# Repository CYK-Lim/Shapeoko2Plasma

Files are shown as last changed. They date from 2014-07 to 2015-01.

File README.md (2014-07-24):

```
Shapeoko 2
	NEMA 23 Mechanical Kit
	Z Axis Upgrade w/ NEMA 23
	Handle/Knob

Probotix
	RF Isolated CNC Breakout Board
	4x SideStep Bi-Polar Stepper Motor Driver
	4x HT23-260-4 Stepper Motor
	24Volt 6.5Amp Switching Power Supply
	6ft. DB25 Male-to-Male Cable
	3x 4" IDC Cable 10-pin
	2x 10PIN 12" IDC Adapter Cable

Hypertherm
	Powermax65
	RS485 Modbus ASCII communications card
	CNC Interface

PC
	Intel i5
	Ubuntu 12.04
	RTAI 3.2 Kernel
	LinuxCNC 2.6
	Parallel Port PCIe card
	RS485 serial port PCIe card
	SheetCAM TNG 6.1

Torch Height Control
	Seeeduino Mega V1.21
	Mesa THCAD Voltage to Frequency converter

Miscellaneous
	Automation Direct Solid state relay
	DIN Rail fuse holder and fuses
	Various cables (2 conductor, 4 conductor, 6 conductor shielded) 
	RS485 breakout board (Amazon)
	Automation Direct ferrule kit

Custom Software
	SheetCAM Post processor (lua)
	Custom M and O commands (Linuxcnc)
	Torch height controls (arduino)
	Modbus ASCII controls and HMI (pyModbus and pyvcp) 

Mechanical additions
	Frame (1”x3” .125” thick mild steel tubing, slots cut with 1/8" wide chop saw blade)
	Slats (1” .125” thick mild steel flats)
	Water basin (24 gauge mild steel sheet bent/welded/coated with Rubberizeit)

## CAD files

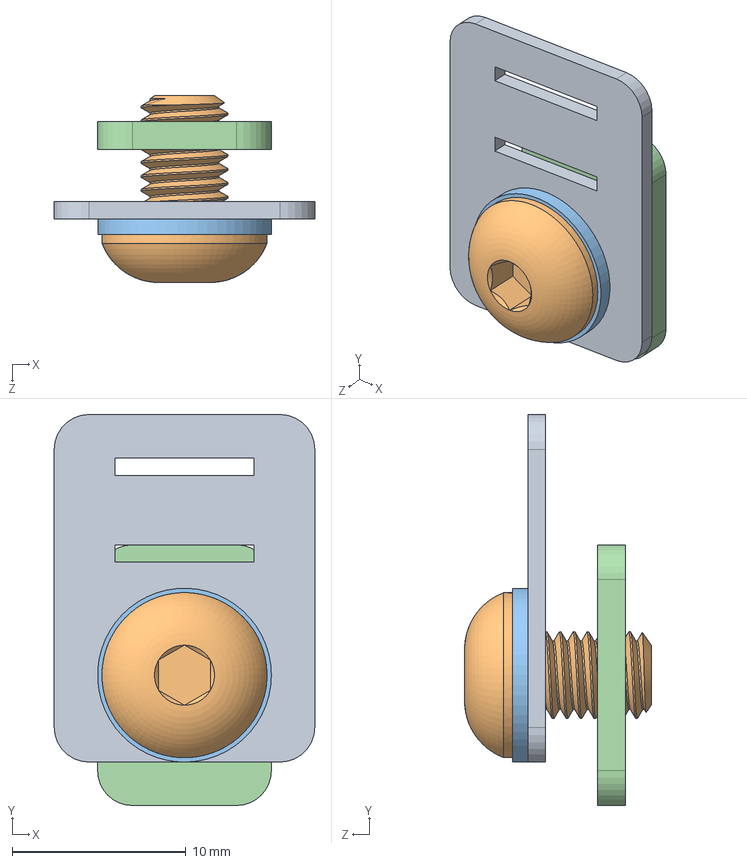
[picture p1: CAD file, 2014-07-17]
Solid Model/belt_clip_assembly.sldasm
15.0 x 22.5 x 10.7 mm
91239A222

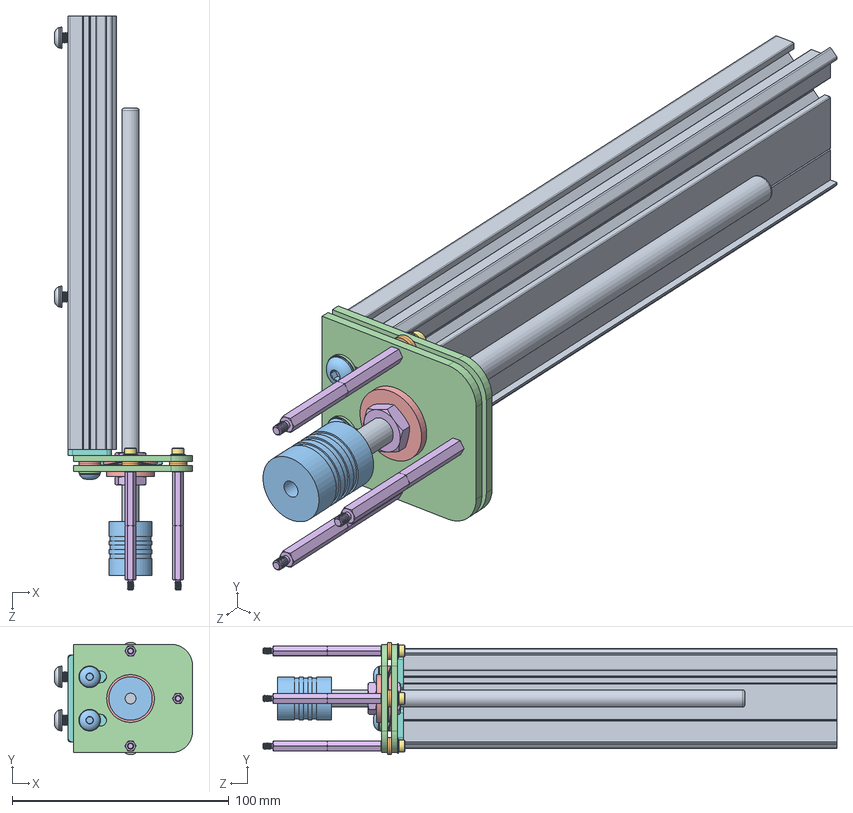
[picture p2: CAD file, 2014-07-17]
Solid Model/S2_Zaxis_500.sldasm
63.8 x 51.8 x 264.7 mm
z-mount_plates x 2
90695A040 x 2
z-axis shim
SM-H05
492-1101-ND x 6
91239A233 x 2
PSM5-01MM x 4
PSBS-50 x 3
9714K630

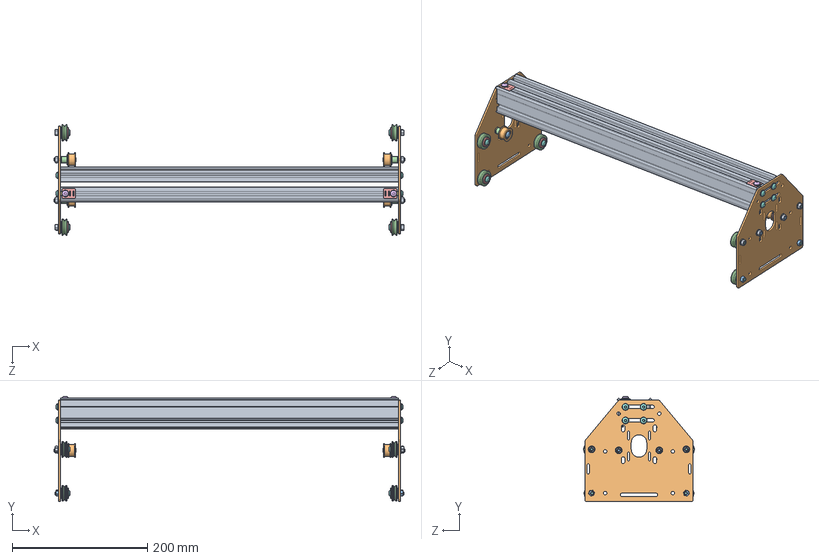
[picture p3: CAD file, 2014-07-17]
Solid Model/S2_Gantry_500.sldasm
518.5 x 155.6 x 163.5 mm
25142-XX500 x 2
B18033 x 4
91239A233 x 8
91239A222 x 2

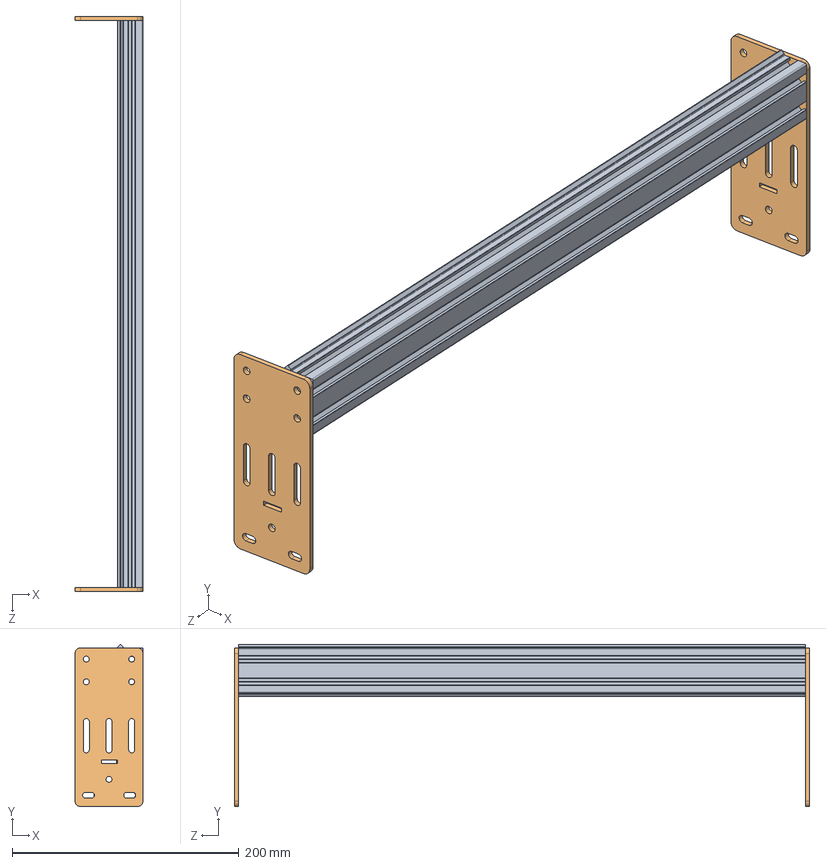
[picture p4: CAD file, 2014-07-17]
Solid Model/Y_Axis_Left.SLDASM
60.0 x 143.0 x 506.8 mm
25142-XX500

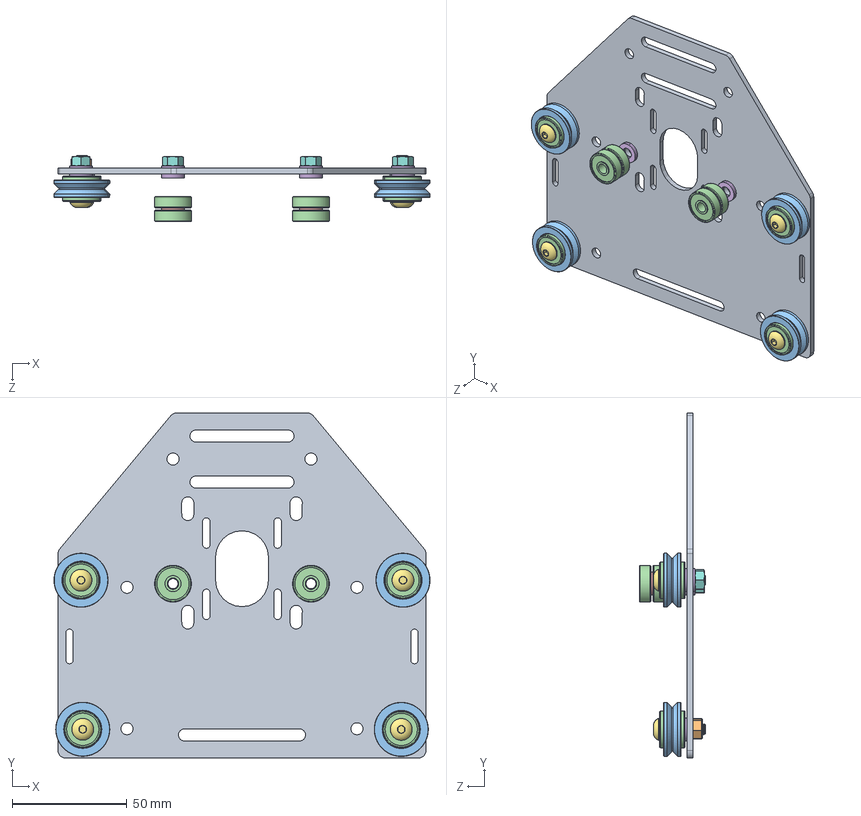
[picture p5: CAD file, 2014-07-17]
Solid Model/plate_assembly_stacked.sldasm
163.5 x 150.0 x 28.8 mm
B18033 x 2
91239A233 x 4

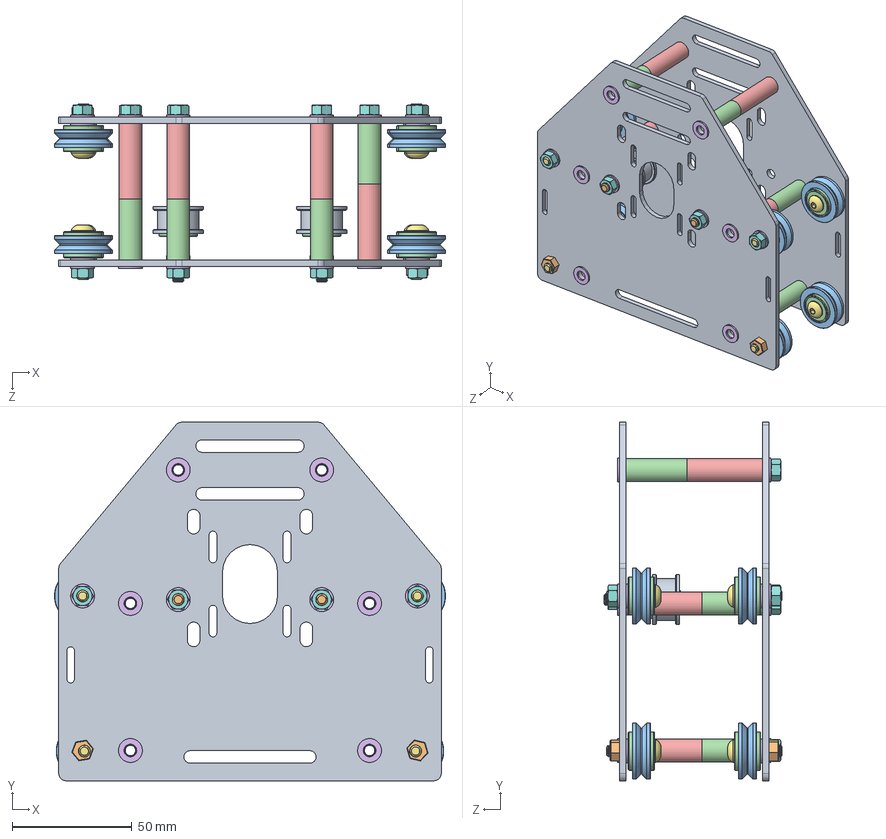
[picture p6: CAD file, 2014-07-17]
Solid Model/ASM_S2_Yaxis_Plates.SLDASM
163.5 x 150.0 x 74.5 mm
B18033 x 4
91239A233 x 8
AS38-12-64 x 6
AS38-12-80 x 6

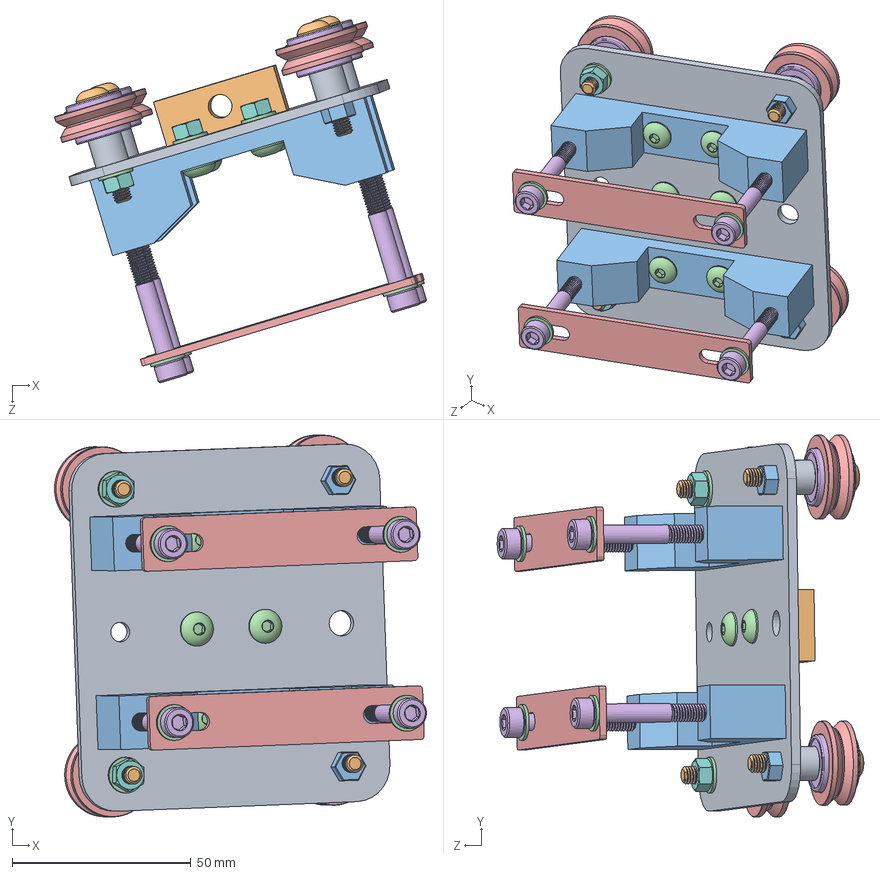
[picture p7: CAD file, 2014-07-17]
Solid Model/ASM_Zaxis_Trolly.SLDASM
104.0 x 106.7 x 102.4 mm
spindle_mount_plate
SM-M08
B18033 x 2
SM-TM x 2
SM-TM2 x 2
91290A260 x 4

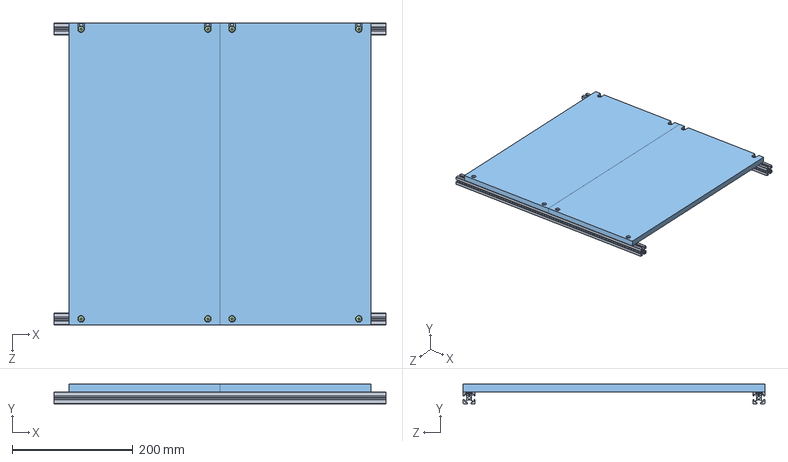
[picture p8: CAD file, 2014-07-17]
Solid Model/S2_Work_Area_500.sldasm
550.0 x 32.7 x 500.0 mm
two_part_wastebaord_500 x 2

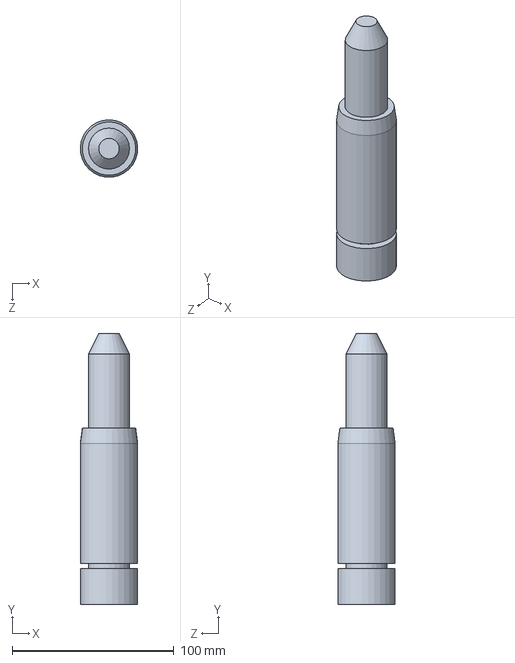
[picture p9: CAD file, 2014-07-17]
Solid Model/Hypertherm Duramax Mini.SLDPRT
35.5 x 167.6 x 35.5 mm

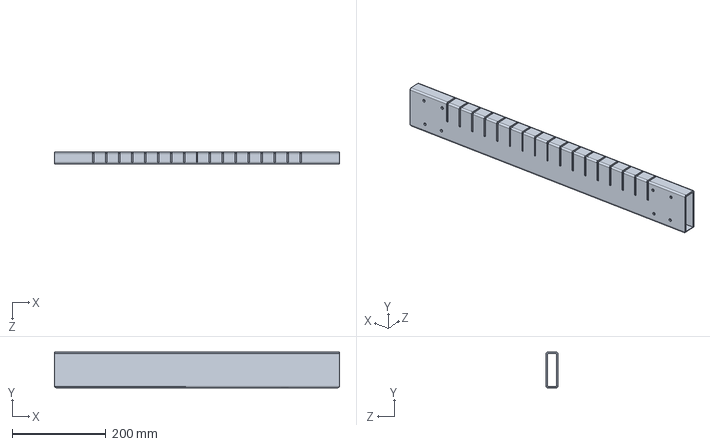
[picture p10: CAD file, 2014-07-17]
Solid Model/1x3x24.SLDPRT
609.6 x 76.2 x 25.4 mm

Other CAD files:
Solid Model/SM-TM.sldprt
Solid Model/PSM5-01MM.sldprt
Solid Model/SM-TM2.sldprt
Solid Model/z-axis shim.sldprt
Solid Model/AS38-12-80.sldprt
Solid Model/SM-M08.sldprt
Solid Model/spindle_mount_plate.sldprt
Solid Model/AS38-12-64.sldprt
Solid Model/25142-07.sldprt
Solid Model/25142-XX500.sldprt
Solid Model/25196-01.sldprt
Solid Model/25197-01.sldprt
Solid Model/25197-02.sldasm
Solid Model/25201-01.sldprt
Solid Model/25202-01.sldprt
Solid Model/25203-02.sldasm
Solid Model/25284-02.sldprt
Solid Model/25285-10.sldprt
Solid Model/25286-01.sldprt
Solid Model/25286-02.sldprt
Solid Model/25286-05.sldprt
Solid Model/25287-02.sldprt
Solid Model/25287-03.sldprt
Solid Model/25312-14.sldprt
Solid Model/25772-02.sldprt
Solid Model/26016-01.sldprt
Solid Model/26028-01.sldprt
Solid Model/26029-01.sldprt
Solid Model/26049-01_550.sldprt
Solid Model/26051-01.sldprt
Solid Model/30169-01.sldprt
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

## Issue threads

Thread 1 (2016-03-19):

using open source 3d printer frimware

mkeyno, 2016-03-19:
hi, thanks for sharing the code , however I was wondering why don't you use the open source 3d printer firmware to control the THC, ? for example you could check state of  the inductive proximity sensor pin before start cutting

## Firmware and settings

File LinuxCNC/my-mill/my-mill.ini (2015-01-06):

# Generated by stepconf at Wed Jun 11 12:59:48 2014
# If you make changes to this file, they will be
# overwritten when you run stepconf again

[EMC]
MACHINE = my-mill
DEBUG = 0x2

[DISPLAY]
DISPLAY = axis
EDITOR = gedit
POSITION_OFFSET = RELATIVE
POSITION_FEEDBACK = ACTUAL
MAX_FEED_OVERRIDE = 1.2
INTRO_GRAPHIC = linuxcnc.gif
INTRO_TIME = 5
PROGRAM_PREFIX = /home/jkl/linuxcnc/nc_files
INCREMENTS = .1in .05in .01in .005in .001in .0005in .0001in
PYVCP = custompanel.xml
GEOMETRY = XYZ

[FILTER]
PROGRAM_EXTENSION = .png,.gif,.jpg Greyscale Depth Image
PROGRAM_EXTENSION = .py Python Script
png = image-to-gcode
gif = image-to-gcode
jpg = image-to-gcode
py = python

[TASK]
TASK = milltask
CYCLE_TIME = 0.010

[RS274NGC]
PARAMETER_FILE = linuxcnc.var
FEATURES = 12

[EMCMOT]
EMCMOT = motmod
COMM_TIMEOUT = 1.0
COMM_WAIT = 0.010
BASE_PERIOD = 25000
SERVO_PERIOD = 1000000

[HAL]
HALUI = halui
HALFILE = my-mill.hal
HALFILE = custom.hal
POSTGUI_HALFILE = custom_postgui.hal

[HALUI]
# add halui MDI commands here (max 64) 



[TRAJ]
AXES = 3
COORDINATES = X Y Z 
LINEAR_UNITS = inch
ANGULAR_UNITS = degree
CYCLE_TIME = 0.010
DEFAULT_VELOCITY = 0.30
MAX_LINEAR_VELOCITY = 5.00

[EMCIO]
EMCIO = io
CYCLE_TIME = 0.100
TOOL_TABLE = tool.tbl

[AXIS_0]
TYPE = LINEAR
HOME = 0.0
MAX_VELOCITY = 5.0
MAX_ACCELERATION = 100.0
STEPGEN_MAXACCEL = 125.0
SCALE = 1014.24
FERROR = 0.05
MIN_FERROR = 0.01
MIN_LIMIT = -0.010
MAX_LIMIT = 11.010
HOME_OFFSET = -0.100000
HOME_SEARCH_VEL = -1.000000
HOME_LATCH_VEL = 0.492980
HOME_IGNORE_LIMITS = YES

[AXIS_1]
TYPE = LINEAR
HOME = 0.0
MAX_VELOCITY = 5.0
MAX_ACCELERATION = 100.0
STEPGEN_MAXACCEL = 125.0
SCALE = 1014.24
FERROR = 0.05
MIN_FERROR = 0.01
MIN_LIMIT = -0.010
MAX_LIMIT = 11.010
HOME_OFFSET = -0.10000
HOME_SEARCH_VEL = -1.000000
HOME_LATCH_VEL = 0.492980
HOME_IGNORE_LIMITS = YES

[AXIS_2]
TYPE = LINEAR
HOME = 0.0
MAX_VELOCITY = 0.824652777778
MAX_ACCELERATION = 10.0
STEPGEN_MAXACCEL = 12.5
SCALE = 19200.0
FERROR = 1
MIN_LIMIT = -4.0
MAX_LIMIT = 4.0
HOME_OFFSET = 0.0

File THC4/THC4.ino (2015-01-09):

/*
 * Timer 3 counts the 1Mhz reference from the THCAD (Port E bit 6)
 * Timer 4 counts the signal from the THCAD (Port H bit 7)
 * Timer 5 controls the output to the stepper driver (pins 45-46)
 * Int4 is the input from the parallel port (pin 2) counting pulses
 * Int5 is the input from the parallel port (pin 3) reading direction
 * Int7 is the input from the parallel port (Port E bit 7) THC ON
 *
 * Created: 5/30/2014 2:10:21 PM
 * Author: owner
 */
 #include <avr/pgmspace.h>
 
 
 
PROGMEM  prog_uint16_t stepToOCR[] = {1830,1828,1826,1824,1822,1820,1818,1816,1814,1812,1810,1808,1806,1804,1802,1800,1798,1796,1794,1792,1790,1789,1787,1785,1783,1781,1779,1777,1775,1773,1771,1769,1767,1765,1763,1762,1760,1758,1756,1754,1752,1750,1748,1746,1744,1743,1741,1739,1737,1735,1733,1731,1729,1728,1726,1724,1722,1720,1718,1716,1715,1713,1711,1709,1707,1705,1703,1702,1700,1698,1696,1694,1692,1691,1689,1687,1685,1683,1682,1680,1678,1676,1674,1673,1671,1669,1667,1665,1664,1662,1660,1658,1657,1655,1653,1651,1649,1648,1646,1644,1642,1641,1639,1637,1635,1634,1632,1630,1628,1627,1625,1623,1621,1620,1618,1616,1615,1613,1611,1609,1608,1606,1604,1603,1601,1599,1598,1596,1594,1592,1591,1589,1587,1586,1584,1582,1581,1579,1577,1576,1574,1572,1571,1569,1567,1566,1564,1562,1561,1559,1557,1556,1554,1552,1551,1549,1548,1546,1544,1543,1541,1539,1538,1536,1535,1533,1531,1530,1528,1527,1525,1523,1522,1520,1519,1517,1515,1514,1512,1511,1509,1507,1506,1504,1503,1501,1500,1498,1496,1495,1493,1492,1490,1489,1487,1486,1484,1482,1481,1479,1478,1476,1475,1473,1472,1470,1469,1467,1466,1464,1463,1461,1459,1458,1456,1455,1453,1452,1450,1449,1447,1446,1444,1443,1441,1440,1438,1437,1435,1434,1432,1431,1430,1428,1427,1425,1424,1422,1421,1419,1418,1416,1415,1413,1412,1410,1409,1408,1406,1405,1403,1402,1400,1399,1397,1396,1395,1393,1392,1390,1389,1387,1386,1385,1383,1382,1380,1379,1378,1376,1375,1373,1372,1371,1369,1368,1366,1365,1364,1362,1361,1359,1358,1357,1355,1354,1352,1351,1350,1348,1347,1346,1344,1343,1342,1340,1339,1337,1336,1335,1333,1332,1331,1329,1328,1327,1325,1324,1323,1321,1320,1319,1317,1316,1315,1313,1312,1311,1309,1308,1307,1305,1304,1303,1301,1300,1299,1298,1296,1295,1294,1292,1291,1290,1288,1287,1286,1285,1283,1282,1281,1279,1278,1277,1276,1274,1273,1272,1271,1269,1268,1267,1265,1264,1263,1262,1260,1259,1258,1257,1255,1254,1253,1252,1250,1249,1248,1247,1245,1244,1243,1242,1241,1239,1238,1237,1236,1234,1233,1232,1231,1230,1228,1227,1226,1225,1223,1222,1221,1220,1219,1217,1216,1215,1214,1213,1211,1210,1209,1208,1207,1206,1204,1203,1202,1201,1200,1198,1197,1196,1195,1194,1193,1191,1190,1189,1188,1187,1186,1184,1183,1182,1181,1180,1179,1178,1176,1175,1174,1173,1172,1171,1170,1168,1167,1166,1165,1164,1163,1162,1160,1159,1158,1157,1156,1155,1154,1153,1152,1150,1149,1148,1147,1146,1145,1144,1143,1142,1140,1139,1138,1137,1136,1135,1134,1133,1132,1131,1130,1128,1127,1126,1125,1124,1123,1122,1121,1120,1119,1118,1117,1116,1114,1113,1112,1111,1110,1109,1108,1107,1106,1105,1104,1103,1102,1101,1100,1099,1098,1097,1096,1094,1093,1092,1091,1090,1089,1088,1087,1086,1085,1084,1083,1082,1081,1080,1079,1078,1077,1076,1075,1074,1073,1072,1071,1070,1069,1068,1067,1066,1065,1064,1063,1062,1061,1060,1059,1058,1057,1056,1055,1054,1053,1052,1051,1050,1049,1048,1047,1046,1045,1044,1043,1042,1041,1040,1039,1038,1037,1036,1035,1035,1034,1033,1032,1031,1030,1029,1028,1027,1026,1025,1024,1023,1022,1021,1020,1019,1018,1017,1016,1016,1015,1014,1013,1012,1011,1010,1009,1008,1007,1006,1005,1004,1003,1003,1002,1001,1000,999,998,997,996,995,994,993,993,992,991,990,989,988,987,986,985,984,984,983,982,981,980,979,978,977,976,976,975,974,973,972,971,970,969,968,968,967,966,965,964,963,962,962,961,960,959,958,957,956,956,955,954,953,952,951,950,950,949,948,947,946,945,944,944,943,942,941,940,939,939,938,937,936,935,934,934,933,932,931,930,929,929,928,927,926,925,925,924,923,922,921,920,920,919,918,917,916,916,915,914,913,912,912,911,910,909,908,908,907,906,905,904,904,903,902,901,901,900,899,898,897,897,896,895,894,893,893,892,891,890,890,889,888,887,887,886,885,884,883,883,882,881,880,880,879,878,877,877,876,875,874,874,873,872,871,871,870,869,868,868,867,866,865,865,864,863,862,862,861,860,860,859,858,857,857,856,855,854,854,853,852,852,851,850,849,849,848,847,847,846,845,844,844,843,842,842,841,840,839,839,838,837,837,836,835,835,834,833,832,832,831,830,830,829,828,828,827,826,826,825,824,823,823,822,821,821,820,819,819,818,817,817,816,815,815,814,813,813,812,811,811,810,809,809,808,807,807,806,805,805,804,803,803,802,801,801,800,799,799,798,797,797,796,795,795,794,794,793,792,792,791,790,790,789,788,788,787,786,786,785,785,784,783,783,782,781,781,780,780,779,778,778,777,776,776,775,775,774,773,773,772,771,771,770,770,769,768,768,767,767,766,765,765,764,763,763,762,762,761,760,760,759,759,758,757,757,756,756,755,754,754,753,753,752,752,751,750,750,749,749,748,747,747,746,746,745,744,744,743,743,742,742,741,740,740,739,739,738,738,737,736,736,735,735,734,734,733,732,732,731,731,730,730,729,729,728,727,727,726,726,725,725,724,723,723,722,722,721,721,720,720,719,719,718,717,717,716,716,715,715,714,714,713,713,712,711,711,710,710,709,709,708,708,707,707,706,706,705,705,704,703,703,702,702,701,701,700,700,699,699,698,698,697,697,696,696,695,695,694,694,693,693,692,692,691,690,690,689,689,688,688,687,687,686,686,685,685,684,684,683,683,682,682,681,681,680,680,679,679,678,678,677,677,676,676,675,675,674,674,674,673,673,672,672,671,671,670,670,669,669,668,668,667,667,666,666,665,665,664,664,663,663,662,662,661,661,661,660,660,659,659,658,658,657,657,656,656,655,655,654,654,654,653,653,652,652,651,651,650,650,649,649,648,648,648,647,647,646,646,645,645,644,644,644,643,643,642,642,641,641,640,640,639,639,639,638,638,637,637,636,636,636,635,635,634,634,633,633,632,632,632,631,631,630,630,629,629,629,628,628,627,627,626,626,626,625,625,624,624,623,623,623,622,622,621,621,621,620,620,619,619,618,618,618,617,617,616,616,616,615,615,614,614,613,613,613,612,612,611,611,611,610,610,609,609,609,608,608,607,607,607,606,606,605,605,605,604,604,603,603,603,602,602,601,601,601,600,600,599,599,599,598,598,597,597,597,596,596,596,595,595,594,594,594,593,593,592,592,592,591,591,591,590,590,589,589,589,588,588,588,587,587,586,586,586,585,585,585,584,584,583,583,583,582,582,582,581,581,580,580,580,579,579,579,578,578,578,577,577,576,576,576,575,575,575,574,574,574,573,573,573,572,572,571,571,571,570,570,570,569,569,569,568,568,568,567,567,567,566,566,565,565,565,564,564,564,563,563,563,562,562,562,561,561,561,560,560,560,559,559,559,558,558,558,557,557,557,556,556,556,555,555,555,554,554,554,553,553,553,552,552,552,551,551,551,550,550,550,549,549,549,548,548,548,547,547,547,546,546,546,545,545,545,544,544,544,544,543,543,543,542,542,542,541,541,541,540,540,540,539,539,539,538,538,538,538,537,537,537,536,536,536,535,535,535,534,534,534,534,533,533,533,532,532,532,531,531,531,531,530,530,530,529,529,529,528,528,528,528,527,527,527,526,526,526,525,525,525,525,524,524,524,523,523,523,523,522,522,522,521,521,521,520,520,520,520,519,519,519,518,518,518,518,517,517,517,516,516,516,516,515,515,515,515,514,514,514,513,513,513,513,512,512,512,511,511,511,511,510,510,510,510,509,509,509,508,508,508,508,507,507,507,507,506,506,506,505,505,505,505,504,504,504,504,503,503,503,503,502,502,502,501,501,501,501,500,500,500,500,499,499,499,499,498,498,498,498,497,497,497,497,496,496,496,495,495,495,495,494,494,494,494,493,493,493,493,492,492,492,492,491,491,491,491,490,490,490,490,489,489,489,489,488,488,488,488,487,487,487,487,486,486,486,486,486,485,485,485,485,484,484,484,484,483,483,483,483,482,482,482,482,481,481,481,481,480,480,480,480,480,479,479,479,479,478,478,478,478,477,477,477,477,477,476,476,476,476,475,475,475,475,474,474,474,474,474,473,473,473,473,472,472,472,472,472,471,471,471,471,470,470,470,470,470,469,469,469,469,468,468,468,468,468,467,467,467,467,466,466,466,466,466,465,465,465,465,464,464,464,464,464,463,463,463,463,463,462,462,462,462,461,461,461,461,461,460,460,460,460,460,459,459,459,459,459,458,458,458,458,458,457,457,457,457,457,456,456,456,456,455,455,455,455,455,454,454,454,454,454,453,453,453,453,453,452,452,452,452,452,451,451,451,451,451,450,450,450,450,450,450,449,449,449,449,449,448,448,448,448,448,447,447,447,447,447,446,446,446,446,446,445,445,445,445,445,445,444,444,444,444,444,443,443,443,443,443,442,442,442,442,442,442,441,441,441,441,441,440,440,440,440,440,439,439,439,439,439,439,438,438,438,438,438,437,437,437,437,437,437,436,436,436,436,436,436,435,435,435,435,435,434,434,434,434,434,434,433,433,433,433,433,433,432,432,432,432,432,432,431,431,431,431,431,430,430,430,430,430,430,429,429,429,429,429,429,428,428,428,428,428,428,427,427,427,427,427,427,426,426,426,426,426,426,425,425,425,425,425,425,424,424,424,424,424,424,424,423,423,423,423,423,423,422,422,422,422,422,422,421,421,421,421,421,421,420,420,420,420,420,420,420,419,419,419,419,419,419,418,418,418,418,418,418,418,417,417,417,417,417,417,416,416,416,416,416,416,416,415,415,415,415,415,415,414,414,414,414,414,414,414,413,413,413,413,413,413,413,412,412,412,412,412,412,412,411,411,411,411,411,411,411,410,410,410,410,410,410,410,409,409,409,409,409,409,409,408,408,408,408,408,408,408,407,407,407,407,407,407,407,406,406,406,406,406,406,406,405,405,405,405,405,405,405,404,404,404,404,404,404,404,404,403,403,403,403,403,403,403,402,402,402,402,402,402,402,402,401,401,401,401,401,401,401,400,400,400,400,400,400,400,400,399,399,399,399,399,399,399,398,398,398,398,398,398,398,398,397,397,397,397,397,397,397,397,396,396,396,396,396,396,396,396,395,395,395,395,395,395,395,395,394,394,394,394,394,394,394,394,393,393,393,393,393,393,393,393,393,392,392,392,392,392,392,392,392,391,391,391,391,391,391,391,391,390,390,390,390,390,390,390,390,390,389,389,389,389,389,389,389,389,388,388,388,388,388,388,388,388,388,387,387,387,387,387,387,387,387,387,386,386,386,386,386,386,386,386,386,385,385,385,385,385,385,385,385,385,384,384,384,384,384,384,384,384,384,383,383,383,383,383,383,383,383,383,382,382,382,382,382,382,382,382,382,381,381,381,381,381,381,381,381,381,381,380,380,380,380,380,380,380,380,380,379,379,379,379,379,379,379,379,379,379,378,378,378,378,378,378,378,378,378,378,377,377,377,377,377,377,377,377,377,377,376,376,376,376,376,376,376,376,376,376,375,375,375,375,375,375,375,375,375,375,374,374,374,374,374,374,374,374,374,374,373,373,373,373,373,373,373,373,373,373,373,372,372,372,372,372,372,372,372,372,372,371,371,371,371,371,371,371,371,371,371,371,370,370,370,370,370,370,370,370,370,370,370,369,369,369,369,369,369,369,369,369,369,369,368,368,368,368,368,368,368,368,368,368,368,367,367,367,367,367,367,367,367,367,367,367,367,366,366,366,366,366,366,366,366,366,366,366,365,365,365,365,365,365,365,365,365,365,365,365,364,364,364,364,364,364,364,364,364,364,364,364,363,363,363,363,363,363,363,363,363,363,363,363,362,362,362,362,362,362,362,362,362,362,362,362,362,361,361,361,361,361,361,361,361,361,361,361,361,360,360,360,360,360,360,360,360,360,360,360,360,360,359,359,359,359,359,359,359,359,359,359,359,359,359,358,358,358,358,358,358,358,358,358,358,358,358,358,357,357,357,357,357,357,357,357,357,357,357,357,357,356,356,356,356,356,356,356,356,356,356,356,356,356,356,355,355,355,355,355,355,355,355,355,355,355,355,355,355,354,354,354,354,354,354,354,354,354,354,354,354,354,354,353,353,353,353,353,353,353,353,353,353,353,353,353,353,353,352,352,352,352,352,352,352,352,352,352,352,352,352,352,351,351,351,351,351,351,351,351,351,351,351,351,351,351,351,350,350,350,350,350,350,350,350,350,350,350,350,350,350,350,350,349,349,349,349,349,349,349,349,349,349,349,349,349,349,349,348,348,348,348,348,348,348,348,348,348,348,348,348,348,348,348,347,347,347,347,347,347,347,347,347,347,347,347,347,347,347,347,346,346,346,346,346,346,346,346,346,346,346,346,346,346,346,346,346,345,345,345,345,345,345,345,345,345,345,345,345,345,345,345,345,345,344,344,344,344,344,344,344,344,344,344,344,344,344,344,344,344,344,343,343,343,343,343,343,343,343,343,343,343,343,343,343,343,343,343,343,342,342,342,342,342,342,342,342,342,342,342,342,342,342,342,342,342,342,341,341,341,341,341,341,341,341,341,341,341,341,341,341,341,341,341,341,341,340,340,340,340,340,340,340,340,340,340,340,340,340,340,340,340,340,340,340,339,339,339,339,339,339,339,339,339,339,339,339,339,339,339,339,339,339,339,339,338,338,338,338,338,338,338,338,338,338,338,338,338,338,338,338,338,338,338,338,337,337,337,337,337,337,337,337,337,337,337,337,337,337,337,337,337,337,337,337,336,336,336,336,336,336,336,336,336,336,336,336,336,336,336,336,336,336,336,336,336,336,335,335,335,335,335,335,335,335,335,335,335,335,335,335,335,335,335,335,335,335,335,335,334,334,334,334,334,334,334,334,334,334,334,334,334,334,334,334,334,334,334,334,334,334,333,333,333,333,333,333,333,333,333,333,333,333,333,333,333,333,333,333,333,333,333,333,333,332,332,332,332,332,332,332,332,332,332,332,332,332,332,332,332,332,332,332,332,332,332,332,332,331,331,331,331,331,331,331,331,331,331,331,331,331,331,331,331,331,331,331,331,331,331,331,331,331,330,330,330,330,330,330,330,330,330,330,330,330,330,330,330,330,330,330,330,330,330,330,330,330,330,329,329,329,329,329,329,329,329,329,329,329,329,329,329,329,329,329,329,329,329,329,329,329,329,329,329,329,328,328,328,328,328,328,328,328,328,328,328,328,328,328,328,328,328,328,328,328,328,328,328,328,328,328,328,327,327,327,327,327,327,327,327,327,327,327,327,327,327,327,327,327,327,327,327,327,327,327,327,327,327,327,327,326,326,326,326,326,326,326,326,326,326,326,326,326,326,326,326,326,326,326,326,326,326,326,326,326,326,326,326,326,326,325,325,325,325,325,325,325,325,325,325,325,325,325,325,325,325,325,325,325,325,325,325,325,325,325,325,325,325,325,325,324,324,324,324,324,324,324,324,324,324,324,324,324,324,324,324,324,324,324,324,324,324,324,324,324,324,324,324,324,324,324,324,323,323,323,323,323,323,323,323,323,323,323,323,323,323,323,323,323,323,323,323,323,323,323,323,323,323,323,323,323,323,323,323,323,322,322,322,322,322,322,322,322,322,322,322,322,322,322,322,322,322,322,322,322,322,322,322,322,322,322,322,322,322,322,322,322,322,322,322,321,321,321,321,321,321,321,321,321,321,321,321,321,321,321,321,321,321,321,321,321,321,321,321,321,321,321,321,321,321,321,321,321,321,321,321,320,320,320,320,320,320,320,320,320,320,320,320,320,320,320,320,320,320,320,320,320,320,320,320,320,320,320,320,320,320,320,320,320,320,320,320,320,320,320,319,319,319,319,319,319,319,319,319,319,319,319,319,319,319,319,319,319,319,319,319,319,319,319,319,319,319,319,319,319,319,319,319,319,319,319,319,319,319,319,318,318,318,318,318,318,318,318,318,318,318,318,318,318,318,318,318,318,318,318,318,318,318,318,318,318,318,318,318,318,318,318,318,318,318,318,318,318,318,318,318,318,317,317,317,317,317,317,317,317,317,317,317,317,317,317,317,317,317,317,317,317,317,317,317,317,317,317,317,317,317,317,317,317,317,317,317,317,317,317,317,317,317,317,317,317,317,316,316,316,316,316,316,316,316,316,316,316,316,316,316,316,316,316,316,316,316,316,316,316,316,316,316,316,316,316,316,316,316,316,316,316,316,316,316,316,316,316,316,316,316,316,316,316,316,315,315,315,315,315,315,315,315,315,315,315,315,315,315,315,315,315,315,315,315,315,315,315,315,315,315,315,315,315,315,315,315,315,315,315,315,315,315,315,315,315,315,315,315,315,315,315,315,315,315,315,314,314,314,314,314,314,314,314,314,314,314,314,314,314,314,314,314,314,314,314,314,314,314,314,314,314,314,314,314,314,314,314,314,314,314,314,314,314,314,314,314,314,314,314,314,314,314,314,314,314,314,314,314,314,314,313,313,313,313,313,313,313,313,313,313,313,313,313,313,313,313,313,313,313,313,313,313,313,313,313,313,313,313,313,313,313,313,313,313,313,313,313,313,313,313,313,313,313,313,313,313,313,313,313,313,313,313,313,313,313,313,313,313,313,312,312,312,312,312,312,312,312,312,312,312,312,312,312,312,312,312,312,312,312,312,312,312,312,312,312,312,312,312,312,312,312,312,312,312,312,312,312,312,312,312,312,312,312,312,312,312,312,312,312,312,312,312,312,312,312,312,312,312,312,312,312,312,311,311,311,311,311,311,311,311,311,311,311,311,311,311,311,311,311,311,311,311,311,311,311,311,311,311,311,311,311,311,311,311,311,311,311,311,311,311,311,311,311,311,311,311,311,311,311,311,311,311,311,311,311,311,311,311,311,311,311,311,311,311,311,311,311,311,311,311,311,311,310,310,310,310,310,310,310,310,310,310,310,310,310,310,310,310,310,310,310,310,310,310,310,310,310,310,310,310,310,310,310,310,310,310,310,310,310,310,310,310,310,310,310,310,310,310,310,310,310,310,310,310,310,310,310,310,310,310,310,310,310,310,310,310,310,310,310,310,310,310,310,310,310,310,310,310,309,309,309,309,309,309,309,309,309,309,309,309,309,309,309,309,309,309,309,309,309,309,309,309,309,309,309,309,309,309,309,309,309,309,309,309,309,309,309,309,309,309,309,309,309,309,309,309,309,309,309,309,309,309,309,309,309,309,309,309,309,309,309,309,309,309,309,309,309,309,309,309,309,309,309,309,309,309,309,309,309,309,309,309,309,309,308,308,308,308,308,308,308,308,308,308,308,308,308,308,308,308,308,308,308,308,308,308,308,308,308,308,308,308,308,308,308,308,308,308,308,308,308,308,308,308,308,308,308,308,308,308,308,308,308,308,308,308,308,308,308,308,308,308,308,308,308,308,308,308,308,308,308,308,308,308,308,308,308,308,308,308,308,308,308,308,308,308,308,308,308,308,308,308,308,308,308,308,308,308,308,307,307,307,307,307,307,307,307,307,307,307,307,307,307,307,307,307,307,307,307,307,307,307,307,307,307,307,307,307,307,307,307,307,307,307,307,307,307,307,307,307,307,307,307,307,307,307,307,307,307,307,307,307,307,307,307,307,307,307,307,307,307,307,307,307,307,307,307,307,307,307,307,307,307,307,307,307,307,307,307,307,307,307,307,307,307,307,307,307,307,307,307,307,307,307,307,307,307,307,307,307,307,307,307,307,307,307,307,307,307,306,306,306,306,306,306,306,306,306,306,306,306,306,306,306,306,306,306,306,306,306,306,306,306,306,306,306,306,306,306,306,306,306,306,306,306,306,306,306,306,306,306,306,306,306,306,306,306,306,306,306,306,306,306,306,306,306,306,306,306,306,306,306,306,306,306,306,306,306,306,306,306,306,306,306,306,306,306,306,306,306,306,306,306,306,306,306,306,306,306,306,306,306,306,306,306,306,306,306,306,306,306,306,306,306,306,306,306,306,306,306,306,306,306,306,306,306,306,306,306,306,306,306,306,306,306,306,305,305,305,305,305,305,305,305,305,305,305,305,305,305,305,305,305,305,305,305,305,305,305,305,305,305,305,305,305,305,305,305,305,305,305,305,305,305,305,305,305,305,305,305,305,305,305,305,305,305,305,305,305,
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
void loop()
{
       

	
	// if there is a new data point available
	if (voltageUpdated)
	{
  		voltageUpdated = 0;
  		calcVolts();
  
                if (thcOn)
                {
  		
        		//voltageERR = voltageSP - voltageACT;
        		
        		if (voltageACT < (voltageSP-deadBand))
        		{
        			thcOffset+=100; // += thcCorrectInc*voltageERR*thcKP;
        		}
        		else if (voltageACT > (voltageSP+deadBand))
        		{
        			thcOffset-=100;// += thcCorrectInc*voltageERR*thcKP;
        		} 
                }
	}

        //be sure the position setpoint is up to date
        if (thcOn)
        {
          currPosSP = currPosIN + thcOffset;
        }
        else
        {
          currPosSP = currPosIN;
        }
	
	
	//Start the output pulsing if it is not already
	if (timer5ON == 0 )
	{			
		if (currPosACT != currPosSP)
		{
			if (currPosACT > currPosSP)
				PORTL |= _BV(PORTL3);//set the direction	
			else 
				PORTL &= ~_BV(PORTL3);//set the direction

    		       //if( thcOn || returnToCmdPos )
                       //{
                        stepIndex = 1; //Speed up
                            
                        newOCR = pgm_read_word_near(stepToOCR + stepIndex);
                            
                        OCR5A = newOCR;
                        OCR5B = newOCR/2;
                       //}	
			
			//start the timer
			TCCR5B |= _BV(CS50); // | _BV(CS50);
			timer5ON = 1;
		}
	}
	
        //LED for troubleshooting
        if( thcOn )
          PORTB |= _BV(7);
        else
          PORTB &= ~_BV(7);
         
         

        
          
	debugJunk();	  //*************************************************** for troubleshooting ***********************************************	
}

//Just for debugging
void debugJunk()
{
  junkCounter++;
  String message = "                             \n";
/*	
	if (Serial.available() )//> 0 && timer5ON == 0)
	{
		incomingByte = Serial.read();
			
		if(incomingByte == '0')
		{
			thcOn = 0;
		}
		else if (incomingByte == '1')
		{
			thcOn = 1;
		}
	}
	
	
*/	
	
		//Serial.print(temp2,BIN);
	
	if (!(junkCounter % 2500))
	{
           
  0        1.00   1.21      0

            //Serial.print(message);
  	  Serial.print(thcOn);
  	  Serial.print("        ");
  	  Serial.print(voltageSP);
          Serial.print("   ");  
          Serial.print(voltageACT);
          Serial.print("      "); 
          Serial.println(thcOffset);
          
        /*Serial.print(thcOn,BIN);
		Serial.print(" ");
		//Serial.print(returnToCmdPos,BIN);
		//Serial.print(" ");		
                Serial.print(voltageSP,2);
		Serial.print(" ");
		Serial.print(voltageACT,2);
		Serial.print(" ");
		Serial.print(thcOffset);
		Serial.print(" ");
		//Serial.print(currPosSP);
		//Serial.print(" ");
		Serial.print(currPosACT);
		Serial.print(" ");
		Serial.println(stepIndex);
*/
	}
	

	//delay(50);
	


	/*
	
	
	temp2 = PINL & _BV(PINL4);
	
	if (temp2 > 0)
	{
		Serial.print("UP");
	}
	else
	{
		Serial.print("DN");
	}
	
	

	//Serial.print(temp2,BIN);
	

		Serial.print(" ");
	Serial.print(timer5ON);
	Serial.print(" ");
	Serial.println(currPos);
	
	delay(10);
	
	*/
	//digitalWrite(13, porte5s);
	



	
	/* 	
	Serial.print(voltage);
	Serial.print("\t ");
	Serial.println(timer4Val);
	Serial.println();
	delay(100);


	digitalWrite(13, HIGH);
	Serial.println("High");
	delay(250);
	digitalWrite(13,LOW);
	Serial.println("Low");
	delay(250);
	*/
}

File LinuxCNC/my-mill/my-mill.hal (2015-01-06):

# Generated by stepconf at Wed Jun 11 12:59:48 2014
# If you make changes to this file, they will be
# overwritten when you run stepconf again
# loadrt trivkins
# loadrt millkins
loadrt tblcompkins
loadrt [EMCMOT]EMCMOT base_period_nsec=[EMCMOT]BASE_PERIOD servo_period_nsec=[EMCMOT]SERVO_PERIOD num_joints=[TRAJ]AXES
loadrt probe_parport
loadrt hal_parport cfg="0xD010 out  "
loadrt stepgen step_type=0,0,0

addf parport.0.read base-thread
addf stepgen.make-pulses base-thread
addf parport.0.write base-thread

addf stepgen.capture-position servo-thread
addf motion-command-handler servo-thread
addf motion-controller servo-thread
addf stepgen.update-freq servo-thread
#net spindle-cmd <= motion.spindle-speed-out
#net spindle-at-speed => motion.spindle-at-speed

net xstep => parport.0.pin-02-out
net xdir => parport.0.pin-03-out
net ystep => parport.0.pin-04-out
net ydir => parport.0.pin-05-out
net zstep => parport.0.pin-06-out
net zdir => parport.0.pin-07-out
net ystep => parport.0.pin-08-out
setp parport.0.pin-09-out-invert 1
net ydir => parport.0.pin-09-out

#############################
# net XSlope => tblcompkins.xslope
# net YSlope => tblcompkins.yslope
# setp tblcompkins.xslope 0.000
# setp tblcompkins.yslope 0.000
#############################


net both-home-y <= parport.0.pin-11-in
net both-home-x <= parport.0.pin-12-in
net estop-ext <= parport.0.pin-15-in


setp stepgen.0.position-scale [AXIS_0]SCALE
setp stepgen.0.steplen 1
setp stepgen.0.stepspace 1
setp stepgen.0.dirhold 25000
setp stepgen.0.dirsetup 25000
setp stepgen.0.maxaccel [AXIS_0]STEPGEN_MAXACCEL
net xpos-cmd axis.0.motor-pos-cmd => stepgen.0.position-cmd
net xpos-fb stepgen.0.position-fb => axis.0.motor-pos-fb
net xstep <= stepgen.0.step
net xdir <= stepgen.0.dir
net xenable axis.0.amp-enable-out => stepgen.0.enable
net both-home-x => axis.0.home-sw-in
net both-home-x => axis.0.neg-lim-sw-in
net both-home-x => axis.0.pos-lim-sw-in

setp stepgen.1.position-scale [AXIS_1]SCALE
setp stepgen.1.steplen 1
setp stepgen.1.stepspace 1
setp stepgen.1.dirhold 25000
setp stepgen.1.dirsetup 25000
setp stepgen.1.maxaccel [AXIS_1]STEPGEN_MAXACCEL
net ypos-cmd axis.1.motor-pos-cmd => stepgen.1.position-cmd
net ypos-fb stepgen.1.position-fb => axis.1.motor-pos-fb
net ystep <= stepgen.1.step
net ydir <= stepgen.1.dir
net yenable axis.1.amp-enable-out => stepgen.1.enable
net both-home-y => axis.1.home-sw-in
net both-home-y => axis.1.neg-lim-sw-in
net both-home-y => axis.1.pos-lim-sw-in

setp stepgen.2.position-scale [AXIS_2]SCALE
setp stepgen.2.steplen 1
setp stepgen.2.stepspace 1
setp stepgen.2.dirhold 25000
setp stepgen.2.dirsetup 25000
setp stepgen.2.maxaccel [AXIS_2]STEPGEN_MAXACCEL
net zpos-cmd axis.2.motor-pos-cmd => stepgen.2.position-cmd
net zpos-fb stepgen.2.position-fb => axis.2.motor-pos-fb
net zstep <= stepgen.2.step
net zdir <= stepgen.2.dir
net zenable axis.2.amp-enable-out => stepgen.2.enable

net estop-out <= iocontrol.0.user-enable-out
net estop-ext => iocontrol.0.emc-enable-in

loadusr -W hal_manualtoolchange
net tool-change iocontrol.0.tool-change => hal_manualtoolchange.change
net tool-changed iocontrol.0.tool-changed <= hal_manualtoolchange.changed
net tool-number iocontrol.0.tool-prep-number => hal_manualtoolchange.number
net tool-prepare-loopback iocontrol.0.tool-prepare => iocontrol.0.tool-prepared

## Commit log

2014-07-17 3D Model
    Initial Commit
    [1x3x24.SLDPRT, 25142-07.sldprt, 25142-XX500.sldprt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]
2014-07-24 updated the torch height controls to include ramping and a separate program just for voltage monitoring.
2014-07-24 added use of new touch probe
2014-07-25 updated THC's and z axis Zero
    [custom.hal, my-mill.ini]
2014-07-30 Digital Output Estop Logic
    Added logic to disable torch and THC outputs from resetting upon etop clear.
    [custom.hal]
2014-07-31 Added more conditionals
    These make sure the torch and THC are only on when they are supposed to be.
    [custom.hal]
2015-01-06 added height compensation for materials that arent level.
    [custom_postgui.hal, my-mill.hal, my-mill.ini]
2015-01-06 Added kinematics file.
2015-01-08 Added electrode wear comp. and feed forward from RT material level comp.
2015-01-08 Fixed quick reverse anomoly
    [THC4.ino]
